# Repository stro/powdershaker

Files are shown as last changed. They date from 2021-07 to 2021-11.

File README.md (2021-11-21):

# PowderShaker -- vibratory addon for Dillon 550/650/750 powder measures

PowderShaker is a small add-on device for Dillon powder measures that helps with uniform powder drop.

It's activated on every drop and uses micro-USB cable to power itself. All components are widely available and the total cost would be around $10.

There are three 3D-printed parts that provide the housing for components and the mount. You'll also need the following components, a soldering gun, and a little bit of skill to assemble it all together:

* Mitsumi R14 mini M20 vibration motor with eccentric wheel ([example](https://www.ebay.com/itm/123180653659))
* USB-powered delay relay ([example](https://smile.amazon.com/dp/B0832MW9L4/)) 
* Micro roller switch ([example](https://www.ebay.com/itm/303542468171))
* 220uF - 330uF electrolytic capacitor (other capacity will work too but you'll need to adjust the timer, larger capacity means longer vibration time)
* 4.7k - 5.6k resistor (other values may work too)
* 5 M4x20 bolts
* 5 M4 nuts
* 2 M2x12 bolts (you can also use M2x16 bolts)
* 2 M2 nuts
* wires

## Assembly instructions:

[See all pictures of major steps in this gallery](https://imgur.com/a/fLLn6EH)

1. Print three parts using PLA+ or similar plastic with the following settings:
    * Layer height: 0.2mm
    * Infill: 20%
    * Support: yes
    * Support join distance: 1mm (only matters for the mount part)

2. Connect V+ to the middle relay connection (COM)
3. Solder the capacitor and resistor in parallel
4. Solder a wire to the negative electrode of the capacitor and connect it to the motor
5. Connect the other motor electrode to NO (normally open) connection
6. Connect the positive electrode of the capacitor to the switch (normally open)
7. Solder the negative electrode of the capacitor to V-
8. Connect TRIG to the switch (common)
9. Affix the switch using two M2x12 bolts with the roller directed outwards
10. Place the relay and the motor in their respective slots
11. Connect the USB cable and verify everything is working correctly. 
12. Adjust the potentiometer on the relay to keep the time when the relay is active around 1.5 or 2 seconds
13. Place the cover on and use two M4x20 bolts and nuts to affix it. Don't apply too much torque.
14. Use two M4x20 bolts and nuts to affix the base to the mount. Nut holes should be looking downwards when everything is assembled.
15. Put the assembled PowderShaker on a Dillon powder measure. Keep in mind that the top part is slightly wider than the bottom.
16. Make sure the powder bar activates the switch on the upstroke.
17. Use M4x20 bolt and nut to tighten the PowderShaker to the powder measure.
18. Connect the USB cable and, using a case, activate the powder drop and check if everything is working correctly.

Use several drops before you start loading to make sure the powder drop is more uniform. If you want to stop using it, simply disconnect the USB cable.

There are two mounts (regular and short). If the regular one places the switch too far away from the bar and doesn't activate it, you may try the short one. 

## Visuals

* [This is how it looks like on the press](https://i.imgur.com/fNcFmbQ.jpg)
* [This is another picture from the side](https://i.imgur.com/8c4y25w.jpg)
* [This is my lousy soldering job](https://i.imgur.com/DSIlx3z.jpg) that shows how it's assembled inside the box
* [This is a gallery of pictures of major assembly steps](https://imgur.com/a/fLLn6EH)
* And finally, [a video of everything in action with powder drop measurings](https://www.youtube.com/watch?v=0ZiXqV_TVxc)

## License AKA **You cannot sell it**

This project is released under Creative Commons Attribution-NonCommercial-ShareAlike 4.0 International (CC BY-NC-SA 4.0) License. What it means to you in just four words?

***You cannot sell it***

You can share and adapt it freely. I cannot revoke these freedoms as long as you follow the license terms, specifically:

* Attribution - you must give appropriate credit
* Non-Commercial - you cannot profit from it
* ShareAlike - if you change something, you must use the same license terms

Full license text can be found at https://creativecommons.org/licenses/by-nc-sa/4.0/legalcode

Copyright (c) 2021 sttek.com

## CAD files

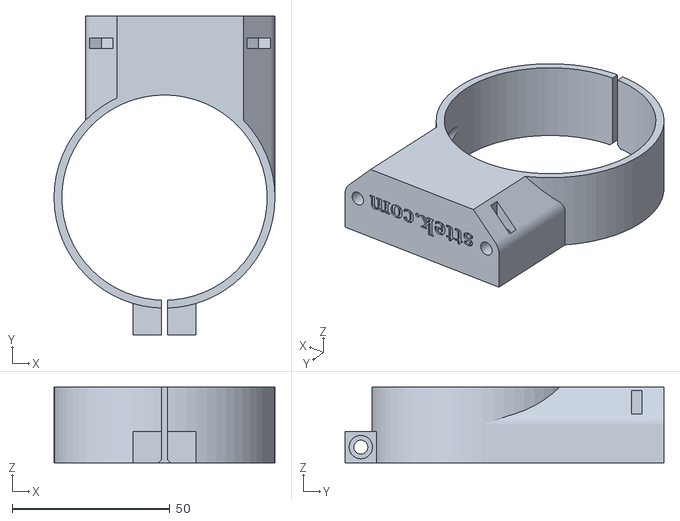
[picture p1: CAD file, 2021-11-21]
PowderShaker-Mount-Short.stl
70.0 x 101.0 x 24.0

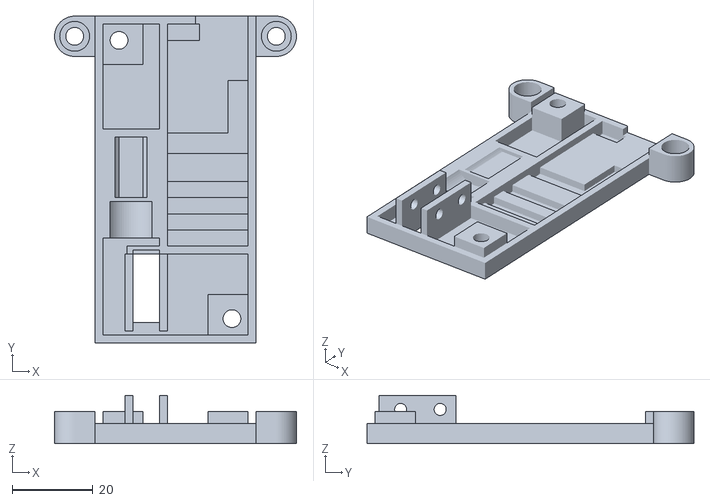
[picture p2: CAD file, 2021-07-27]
PowderShaker-Base.stl
60.0 x 81.0 x 12.0

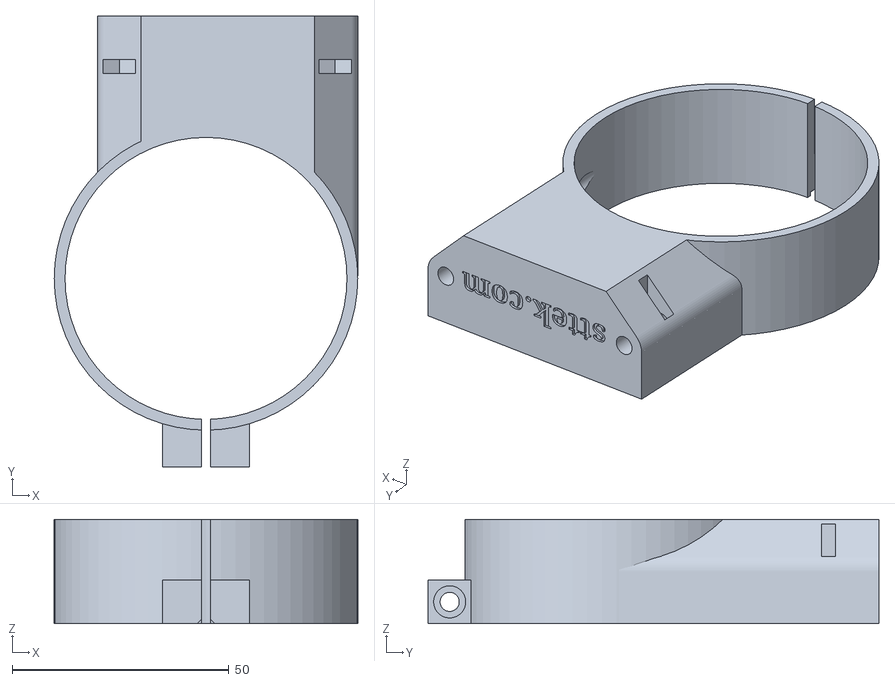
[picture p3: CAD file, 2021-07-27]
PowderShaker-Mount.stl
70.0 x 104.0 x 24.0

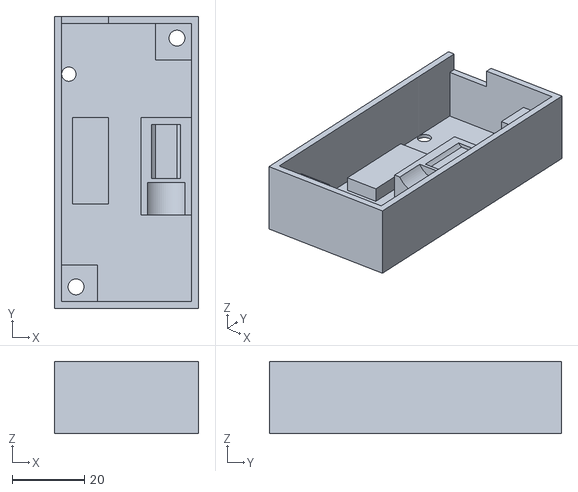
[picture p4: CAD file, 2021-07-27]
PowderShaker-Cover.stl
40.0 x 81.0 x 20.0

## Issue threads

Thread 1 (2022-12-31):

Relay problems

RonnmarkB, 2022-12-31:
Good day

I have built two of theese shakers, however I have encountered some problems. On both builds, the timer isn't consistent. Once activated, the shaker may run for 2 or for 5 seconds, this issue appears to be random. Once in a while the relays also "clicks".

For example, switch is triggered and run time on vibrator may be as follows (timer is not adjusted in between)

2s
1,5s
4s
0,5s
2s
etc

Do you have any idea why I'm having this issue? I'm using 5,1k ohm and 220uF.

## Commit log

2021-07-30 Updated assembly instructions with pictures
2021-11-21 Added short mount
    [PowderShaker-Mount-Short.stl]
